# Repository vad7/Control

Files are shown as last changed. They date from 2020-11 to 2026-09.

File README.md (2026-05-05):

# ControlHeatPump
Контроллер теплового насоса

Открытый проект "Народный контроллер" для тепловых насосов.<br>
Данное програмноое обеспечение предназначено для управления<br>
различными типами тепловых насосов для отопления и ГВС.<br>
<br>
В данном репозитории идет текущая работа, возможны ошибки и нестабильная работа.<br>
Несколько оттестированный релиз здесь: https://github.com/vad7/ControlHeatPump<br>
<br>
Подробное обсуждение проекта на форуме: <br>
https://www.forumhouse.ru/threads/352693/ <br>
https://www.forumhouse.ru/threads/437182/ <br>
https://www.forumhouse.ru/threads/492563/<br>

Изменения по версиям: <br>
Версия 1.216<br>
1. Предварительный нагрев трассы котла по времени и по температуре, отложенное включение теплого пола по температуре
2. Доработка Modbus
3. рефакторинг кода
Версия 1.207<br>
1. Котел электрический или газовый. Управление через адаптер EctoControl RS485 (Modbus) или реле или Модбас реле. Возможность настроить раздельные цели для котла и ТН<br>
2. Динамические картинки на схеме.
3. Рефакторинг кода, оптимизация веба, отказ от семафоров RTOS, PID для охлаждения
4. Возможность греть бойлер только тэном
5. Мониторинг и информирования о ошибках и состояния нескольких BMS АКБ (входной программный UART на скорости 333 бод)
Версия 1.200<br>
1. Поддержка символьного дисплея 20x4 символов (LCD2004), может работать совместно с Nextion.<br>
2. ТН Воздух-Вода - полная поддержка, разморозка, установка оборотов компрессора и ЭРВ.<br>
3. Ежесуточные реле - переключение по температуре и по ночному тарифу<br>
4. Дамп ячеек Modbus, загрузка файла дампа в устройство Modbus<br>
5. Частотник Vacon: управление вентилятором, настройка мощности, контроль температуры, авто-сброс ошибки связи<br>
6. Дисплей Nextion: описание ошибки ТН текстом на главном экране<br>
7. Исправление множества ошибок в функциях: EEV, WR, Vacon, COP, Pumps, web<br>
8. Корректировка ЭРВ при переходе отопление-бойлер<br>
9. Опция включения циркуляционного насоса ГВС по расписанию<br>
10. Возможность изменять аварийные границы датчиков температур через веб<br>
11. Ограничение оборотов компрессора по времени<br>
12. ГВС: использовать только тэн во время "расписание только для тэна"<br>
13. Не считать статистику с меткой "во время работы" в переходных моментах бойлер-отопление и при возврате масла<br>
14. Статистика - отдельно считается тэн бойлера<br>
15. Пересоздание stats файлов при ошибке последовательности или длине=0<br>
16. Исправление работы насосов в паузе<br>
17. Исправление синхронизации времени, запрет смены часов во время работы ТН<br>
18. Исправление скролбара в веб<br>
19. Опция запрещать смену конкретного расписания<br>
20. Исправление безопасного доступа через веб, из-за кэширования он не работал адекватно<br>
21. Опция продолжения отопления после нагрева бойлера, если внутри гистерезиса<br>
22. Отображение на веб о включении суточных реле<br>
23. Корректировка минимальной мощности ваттроутера в зависимости текущей мощности с MPPT<br>
24. Поддержка двунаправленного электро-счетчика DDS238-2 ZN/S<br>
25. Настройки насосов отопления и дополнительного тэна перенесены в профили<br>
26. Новый режим работы дополнительного тэна на выходе ТН - интеллектуальный, теперь их три: по дому, по улице, интеллектуально<br>
27. Температура цели бойлера на схеме<br>
28. Корректировка датчиков WiFi (esp8266)<br>
29. Нагрев бойлера во время отсутствия электричества, если есть солнце<br>
30. Перенос настройки выключения насоса после останова компрессора в профили, отдельная задача по управлению насосами, чтобы была возможность контроля температур цели.<br>
31. Автопереключение режима работы - Отопление / Охлаждение<br>
32. Возможность использовать несколько периодов включения одного и того же ежесуточного реле.<br>
33. Возможность задать дополнительно любой датчик температуры как цель отопления. Расписание по часам контроля этих датчиков для каждого профиля.<br>
34. Догрев бойлера тэном во время паузы компрессора и низкой температуры или когда не смог нагреть с первого раза<br>
35. Управление теплым полом по датчикам теплого пола. Два режима - по превышению на заданную дельту целевой температуры или по целевой температуре датчика.<br>
36. Старт нагрева по минимальной температуре подачи.<br>
37. Максимальная температура цели для принудительного останова цикла нагрева, если по другим датчикам еще нужно греть.<br>
38. Поддержка частотников Danfoss VLT, Danfoss Micro Drive FC-51.<br>
39. Управления дополнительным солнечным подкачивающим инвертором (через реле).<br>
40. Подсчет потребления по дневному/ночному тарифу раздельно, опциональное.<br>

<br>
Версия 1.018-1.096<br>
1.  Исправление ошибок, оптимизация, доработка библиотек<br>
2.  Управления теплым полом (RPUMPFL), по выбранным датчикам температуры<br>
3.  Опции по догреву бойлера<br>
4.  Отправка SMS на smsc.ua, gate.smsclub.mobi<br>
5.  Для дисплея Nextion - cтраница изменения профилей, отображение реле бойлера, работа от генератора<br>
6.  Аналоговое или ШИМ управление частотником (используется класс VACON)<br>
7.  Добавлен Serial4<br>
8.  Загрузка веба на SD<br>
9.  Инвертор Омрон - обновление программирования и описания<br>
10. Отладка через Native USB порт (#define DEBUG_NATIVE_USB)<br>
11. Ежесуточное включение реле по расписанию (в режиме отопления)<br>
12. Поддержка электросчетчика PZEM-004T v3 (#define USE_PZEM004T)<br>
13. Добавлен режим работы ТН от резервного источника питания (генератора)<br>
14. Управление краном солнечного коллектора<br>
15. Улучшение режима супербойлера<br>
16. Поддержка NTC датчиков температуры (например: NTC 10K, B3435, резистор к VCC 15к)<br>
17. Вывод расширенной инфы по датчикам DS18B20<br>
18. Усиление на АЦП канале (x1,x2,x4) - #define ADC_GAIN<br>
19. Настройка графиков вынесена в конфиг, возможность изменить графики по датчикам во время работы<br>
20. Сохранение/восстановление настроек в bin всех профилей<br>
21. Работа от генератора: ограничение частоты, авто-определение источника<br>
22. Настройка погодозависимости целевой температуры<br>
23. Автопереключение расписаний по месяцам, погодозависимость<br>
24. Страницы помощи в веб<br>
25. Информирование по HTTP других контроллеров дома о работе от генератора<br>
26. Автозапуск генератора, гистерезис при работе от генератора<br>
27. Ваттроутер (PWM, реле, HTTP реле)<br>

Версия 0.967-1.017<br>
1.	Оптимизирован и уточнен алгоритм расчета температуры фреона по давлению<br>
2.	Фреон теперь задается через config.h (#define FREON)<br>
3.	Изменен формат TRANsADC[ANUMBER] в config.h, теперь целое число в тысячных<br>
4.	Отображение активного расписания<br>
5.	Добавлено инвертирование реверсивного клапана (#define INVERT_TRV)<br>
6.	Добавлен график переохлаждения<br>
7.	Контроль потока с учетом супербойлера<br>
8.	Настройка дельты включения СК<br>
9.	Документация на частотник по кнопке "?"<br>
10.	Переход на библиотеку SAM 1.6.12<br>
11.	Шаги закрытия ЭРВ задаются через #define EEV_CLOSE_STEP<br>
12.	Кнопка "подготовка к обновлению" - установка ЭРВ, сохранение буферов и т.д.<br>
13.	Для конфигурации без датчика высокого давления (PCON) добавление графиков "Конденсации" и "Нагнетание-конденсация"<br>
14.	Возврат масла для частотников Vacon<br>
15.	Отключение принудительной циркуляции ГВС при нагреве ГВС в режиме супербойлера<br>
16.	Очистка графиков при старте ТН (#define CLEAR_CHART_HP_ON)<br>
17.	Алгоритм прямого управления ЭРВ без ПИДа, контроль перегрева на входе компрессора<br>
18.	Защита от "заливания компресора"<br>
19.	Добавлена опция NO_MIN_EEV_CONTROL - При работе ПИД ЭРВ не контролировать достижение минимального открытия<br>
20.	График Нагнетание-Конденсация<br>
21.	Режим нагрева бойлера вместе с отоплением<br>
22.	Добавлено ограничение роста частоты ПИД регулятора<br>
23.	Графики поминутной работы на SD карте<br>
24.	Статистика по дням на SD карте, график с экспортом<br>
25.	Алгоритм 2 для ПИД регулятора (#define PID_FORMULA2)<br>
26.	Попытка восстановления соединений по модбасу перед пуском<br>
27.	Контроль останова частотника Vacon, уменьшение лога диагностики W5500<br>
28.	Проверка выключения инвертора ОМРОН через дискретный выход<br>
29.	Добавлена проверка исправности ЭРВ<br>
30.	Оптимизация задач RTOS<br>
31.	Подстройка температуры без смены профиля в расписаниях<br>
32.	Корректировка потребляемой мощности по включению реле<br>
33.	Исправление ошибок, оптимизация, доработка библиотек<br>
<br>
Версия 0.966<br>
1. Обновление текстовых файлов<br>
2. Добавлено описание ТН, исправлены ошибки для компиляции 1 конфига<br>
3. Работа над статистикой с записью ее на SD карту<br>
4. Фикс бага инициализации nextion если он находится в спящем режиме<br>
5. Мелкие уточнения в веб морде<br>
6. Обновление 2 конфига и уточнение типа ошибки при пуске компрессора<br>
7. Добавлен еще один алгоритм разморозки без датчика разморозки по температурам. Автор Pskovsat<br>
<br>
Версия 0.965<br>
1. Реализована возможность загрузки и работы с веб мордой на чипе spi flash.В опциях есть флаг загрузки из него<br>
2. Оптимизация работы АЦП<br>

Версия 0.964
1. Исправления ошибок в алгоритме работы ТН
2. Оптимизация работы АЦП
3. Оптимизация функции прерывания АЦП

Версия 0.963
1. Добавление spi диска
2. Частично сделана загрузка файлов через веб в spi диск (еще нужно причесать код и контроль ошибок)
3. Опция переключения места хранилища для веб-сервера
4. Доделка загрузки веб морды через веб в spi диск Есть проблемы при загрузке множества файлов (потеря пакетов)
5. Обновление дисплея Nextion, включая его прошивку
6. bugsfixs, добавлен редактор Nextion
7. Оптимизация длин неоторых запросов
8. Оптимизация стека RTOS

Версия 0.962
1. Изменены: структура сохранения, библиотека RTC, нумерация профилей в вебе, и др.
2. Nextion code changed
3. Nextion class rework
4. Исправлена ошибка с выводом сообщений при ошибках в классе HeatPump
5. Расписание теперь всегда компилится
6. Начало работы над загрузкой веб морды в spi Сделано декодирование имени и размера загружаемого файла
7. Сделан для post запросов разбор заголовка определение имени и длины файла и определение размеров первого (принятого) куска файла
8. Nextion update

Версия 0.961
1. Перенос SPI_RATE -> config.h
2. Замена библиотеки SdFat, функция тестирование скорости SD карты (/TEST_SPEED:<имя файла>)
3. Оптимизации библиотеки SdFat
4. Установка скорости SD в МГц - #define SD_CLOCK 24

Версия 0.960
1. Поддержка ИБП на контроллер
2. На страницу "Файлы" добавлены элементы для выбора файлов для копирования в spi eeprom
3. Исправлена ошибка с upload files
4. Имена аналоговых датчиков перенесены в config
5. Исправление ошибки вывода на график частотных датчиков
6. Добавлена опция - СК регенерирует ГК в простое ТН
7. Оптимизация закладки тест
8. Оптимизация СК, конфиг vad7, дефайн DEBUG_MODWORK
9. Настройки СК

Версия 0.959
1. Оптимизация web, выложена схема платы Добрыни
2. Замена в SDK DUE - добавлен класс UART
3. Исправлена ошибка с RPUMPBH
4. Исправлена ошибка с radio_sensor
5. Добавлена схема K-Line адаптера, небольшие фиксы
6. Исправлена ошибка с edit strings

Версия 0.958
1. Солнечный коллектор на плане (картинка)
2. Обновление первого конфига до текущей версии (cтарт-стоп компрессор с ТРВ переливная схема)
3. Включенное реле вручную на странице тестирование можно выключить только на ней, в не зависимости от текущей или будующей работы ТН.
4. Настройка через Config.h какие датчики температуры выводить на страницу "Схема", в const uint8_t SENSORTEMP[TNUMBER]={...} нужно поставить 2, у нужного датчика.
5. Изменение целевых температур бойлера и отопления на дельту по часам, для эффективного использования ночного тарифа
6. Условие расчета КОП (работа компрессора) определяется #define COP_ALL_CALC
7. На github выложена информация по дисплею Nextion
8. На github выложена информация по WiFi устройству (датчик температуры)
9. Проверка состояния частотника только перед его непосредственным стартом.
10. Добавлена опция "Однократный поиск "0" ЭРВ" Настройки ЭРВ из "Опций" перенесены в "Настройки ЭРВ"
11. Оптимизация парсера для вывода графика
12. "Причесывание" надписей на веб морде
13. Фикс бага для датчиков Wifi (откат формата uptime к виду 00d 00h 00m) Обновление морды удаленного датчика wifi
14. Оптимизация веб (датчики), температура
15. Поддержка радиодатчиков ZONT МЛ‑703

Версия 0.957
1. Опция "теплый пол" в профилях - управляет насосом RPUMPFL
2. Опция - расписание ГВС только для ТЭНа бойлера
3. Изменение режима турбо ГВС. Теперь при включении турбо+догрев ГВС греетеся ТН+ТЭН до температуры догрева далее только ТЭН
4. Фикс работы насосов (в схеме без трехходового) для режима пауза
5. Чтение настроек из файла (в новом формате)
6. Фикс алгоритма Сальмоннеллы
7. Фикс блокировки семафорора для 485 порта (уменьшена загрузка CPU при работе ТН)
8. Фикс сброса сетевой карты
9. Добавлена возможность работы с солнечным/воздушным коллектором (#define USE_SUN_COLLECTOR)

Версия 0.956
1. Оптимизирована запись в журнал, радиодатчики - начало.
2. max/min sensorADC
3. Включение RPUMPO при переключение с бойлера на отопление
4. Фикс ошибки при выходе из нагрева ГВС при срабатывании защиты
5. Cохранение в файл в новом формате
6. Опция логировать работу частотника
7. Фикс при переходе нагрева бойлера на тэн
8. Опциональное вычисление для TIN среднего и/или минимального значения среди других датчиков
9. Фикс расчета перегрева при охлаждении, фикс работы бойлера (переключение на дом)

Версия 0.955
1. Оптимизация работы oneWire
2. Ускоренный поиск датчиков температуры
3. Неограниченное кол-во DS18x20, исправление ошибки в DUE UART

Версия 0.954
1. Оптимизация графиков
2. Ethernet lib fix (зацикливание при передаче MQTT)
3. Расчет графиков powerCO powerGEO на лету, фикс вывода графиков в файл
4. Синхронизация времени по HTTP GET с esp8266 веб-сервера (отдельное устройство vad711),
5. Изменен блок статусов, опция не проверять CRC у DS18B20, изменены единицы работы насосов в паузе на сек, изменены настройки датчиков протока, багфиксы.
6. Индикация тэна и насоса бойлера на странице схема, багфиксы
7. Возможность использовать 4 шины датчиков температуры, 3 из них могут быть двухпроводные.
8. В файл настроек в текстовом виде, добавлен вывод новых (пропущеных) параметров
9. Доработка по шинам температуры на DS2482, добавлен режим чтения аналоговых датчиков через модбас
10. Фикс разморозки воздушника + описание в части датчиков температуры
11. Сохранение без потери настроек при изменении структуры
12. Поддержка датчиков ds18s20

Версия 0.953
1. Веб морда добаление дополнительных параметров на схему ТН
2. Возможность скрытия логирования ошибок чтения счетчика SDM120
3. Оптимизация библиотеки Модбас в части работы с портом
4. Дополнительные флаги для датчиков температуры (логирование и игнорирование ошибок)
5. Оптимизация чтения датчиков и modbus, вывод частоты сети 220 в веб.
6. Вывод мощности CO, доработка Vacon
7. Доработка корректировки перегрева, исправление ошибок  модбас, ваком
8. Оптимизация парсера - удаление из парсеров параметров которые только на чтение
9. Фикс восстановления настроек инвертора Омрон (флаги)
10. Небольшие переделки страницы ЭРВ
11. Добавлен график 20, 30 сек, небольшая оптимизация парсера
12. Фикс для охлаждения датчик TCONOUT и фикс расчета мощностей и СОРов для охлаждения
13. Доработка корректировки перегрева
14. Оптимизации работы с ftoa itoa, удаление функции int2str
15. В config настройка задержки после переключения насосов
16. Оптимизация чтения счетчика SDM
17. Оптимизация функций DecodeTimeDate и StatDate, фикс ошибок парсера реле
18. Фикс ошибки старта насоса при догреве(только)
19. Расчет мощностей и СОР всегда (раньше было только при работе)
20. Vacon расчет номинальной мощности
21. Доработка страницы ЭРВ, фикс ПИД эрв
22. фикс передачи на MQTT сервер
23. Мощность частотника в Вт
24. Vacon - авто-очистка сбоя, очередь из 1 команды, оптимизация, раздельный останов насосов по дефайну и др.
25. Возможность выключить ТН из отложенного запуска/рестарт по ошибке
26. Для Омрона отдельная страница настроек (гц) - надо копировать
27. Перенос флага включения ТН в счетчики, теперь профиль реже пишутся
28. Дельта коррекции перегрева считается от стартового перегрева

Версия 0.952
1. Добавлено в управление ЭРВ возможность корректировки перегерва в зависмости от разницы температур испарителя и конденсатора
2. Оптимизация сохранения ЭРВ
3. Фикс: DHСP, датчики температуры. Оптимизация веба.
4. Опция - один датчик на 2-ой шине 1-Wire, для уменьшения влияния помех (измененен формат сохранения: 123)
5. DNS по TCP (выбор автоматически), доработка сетевой либы, оптимизация журнала и др.
6. Начало переделки парсера запросов с целью его оптимизации и увеличения скорости.
7. В класс ЭРВ добавлы настройки (из дефайнов) и оптимизировано сохранение (единая структура настроек)
8. В класс FC добавлы настройки (из дефайнов) и оптимизировано сохранение (единая структура настроек) (измененен формат сохранения: 125)
9. В опции ТН добавлены настройки времен, парсер опций переделан

Версия 0.951
1. Доработка веб, перенос настроек в config, исправление багов
2. Доработка страницы тестирования
3. Добавлен расчет переохлаждение на схеме ТН

Версия 0.950
1. Доработка 1-Wire, багфиксы, новая ошибка ERR_ONEWIRE_RW - ошибка во время чтения/записи OneWire
2. Фикс библиотеки DUE для доступности портов D53,D69
3. Доработка I2C init
4. Оптимизация Web-modbus

Версия 0.949
1. Оптимизация использования стека в itoa, vsnprintf, ftoa cj,собсвенная функция printf
2. Patch Arduino board SAM library for optimized itoa() function
3. Добавлен насос нагрева ГВС RPUMPBH (не циркуляции ГВС)
4. Фикс отображения включения ТН во время паузы
5. Добавлена кнопка сброса статистики задач free RTOS
6. Исправлена ошибка перехода в режим Ожидания по расписанию
7. Для экономии памяти теперь графики расчета разности температур ПТО рассчитываются в момент запроса
8. Добавлен насос теплых полов RPUMPFL (в режиме охлаждения не включается)
9. Перевод FLOWPCON в не обязательный параметр
10. Автоскрытие аналогового управления инвертером, насоса ТП
11. Доработка по инвертору Vacon (режим тест)

Версия 0.948
1. Уменьшение потребление стека RTOS
2. Фикс ожидания DHCP, оптимизация сетевой либы

Версия 0.947
1. При инициализации сетевого чипа добавлена проверка на соединение сетевым кабелем (link)
2. Переделан код обслуживания ТЭНа бойлера, теперь он сосредоточен в одном месте
3. Оптимизация и переименование кода для переключения между ГВС и отоплением/охлаждением (поддержка управления насосами для переключения)
4. Исправлена ошибка с сохранением/восстановлением настроек в бинарный файл
5. Доделана и протестирована страница Modbus (можно читать/сохранять регистры)
6. Сделан алгоритм обеззараживания (сальмонелла) для ГВС
7. Исправлена ошибка в расписании ГВС

Версия 0.946
1. Исправлена ошибка отображения графика потока конденсатора
2. Исправлена ошибка вывода в текстовый файл настроек (коэффициент для аналогового датчика)
3. Исправлена ошибка управленем догревом бойлера - алгоритм перенесен в другое место
4. Исправлена ошибка в режиме тест для датчиков потока
5. Настройки догрева бойлера перенесены в раздел ГВС из опций (откорректированы имена параметров запросов)
6. Сделан вывод специфических ошибок для Vacon 10 и пофиксены некоторые ошибки
7. Добавлена возможность проверки потоков на минимальные значения перед включением компрессора (#define FLOW_CONTROL)
8. Доработана морда для сканирования после изменения работы шины OneWire, в новой версии увеличилось время сканирования.
9. Дмитрий обновил мобильную морду
10. Добавлен функционал модификации имен запрашиваемых файлов, теперь в зависимости от конфига показываются на морде разные схемы.
11. В работу ТН добавлены внутренние команды WAIT и RESUME для обеспечения функционала расписания, теперь если в расписании дырка (нет профайла) то ТН будет находится в сосоянии "Ожидание"
12. ТЕСТ страничка с чтением/записью произвольных ячеек Modbus RTU

Версия 0.945
1. R3WAY переведен в необязательный, теперь можно компилировать без него
2. При переключениеи с ГВС сделано временное отключение (#define DELAY_BOILER_OFF) части защит, на время остывания ТН.
3. Немного переделана функция вывода ошибок, теперь где актуально выводится имя функции в которой произошла ошибка
4. В уведомлениях почты убран вывод устройство которых нет в текущей конфигурации (если стоит флаг выводить подробности)
5. Исправлен и добавлен вывод настроек ТН в текстовом виде (дабавлены настроки тарифов)
6. Проведено переименование констант, переменных и функция инвертора  в нейтральные (без упоменния ОМРОН и МХ2)
7. Добавлена поддержка трехфазного счетчика SDM630 (vad711) (определить #define USE_SDM630)
8. Класс частотный преобразователь был стандартизован (все аппартано зависимые функции спрятаны внутрь класса) для возможности подключения других инверторв короме Omrona
9. vad711 добавил поддержку инвертора Vacon 10 по модбасу.
10. Исправлена ошибка подсчета общего числа ошибок чтения датчиков температуры
11. Переделана блокировка задачи циркуляционного насоса отопления в паузах
12. Исправлена ошибка вывода информации при старте ТН
13. Переделан механизм работы с датчиками температуры. Теперь разрешено три вида шин OneWire и одновременно может присутвовать три вида шин в контроллере.
14. Добавлено расписание работы (пока не до конца)
15. Переделан вид расписания бойлера на веб морде
16. Добавлена страница на вебморду для вывода информации по задачам операционной системы (главное - минимальный размер стека)
17. Часть нагрузки из задачи "бездействия" перенесено в задачу чтения датчиков
18. На морде в профилях сделано обновление данных при изменении параметров профиля
19. В связи с работой над расписаниями, удален функционал тарифов день/ночь
20. Исправена ошибка вывода числа ошибок чтения температурных датчиков.
21. Добавлен ввод теплоемкости теплоносителя в контурах где стоят расходомеры (изменилась версия сохранения)
22. Переделана размерность коэффициентов пересчета расходомеров, теперь она в имп/литр

Скриншеты веб-интерфейса:

Состояние
Схема
ЭРВ
Настройки
Расписание
Датчики
Реле
Инвертор
RTOS
Графики
Графический лог
Статистика
Ваттроутер

Выносной экран Nextion:

Nextion Main
Nextion Scheme
Nextion Heat

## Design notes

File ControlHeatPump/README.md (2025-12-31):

# Control
Heat pump full repository

<br>
<b>Ver. 1.207<b>

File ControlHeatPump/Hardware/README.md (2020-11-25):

# ControlHeatPump
Файлы которые надо заменить в стандартном SDK Due (смотрите путь к файлам начиная с hardware)<br>
Библиотека DUE SAM: https://github.com/arduino/ArduinoCore-sam

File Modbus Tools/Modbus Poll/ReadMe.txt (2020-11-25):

------------------------------------------------------------------------------------
                       Modbus Poll
         Copyright (c) 2002-2017. Witte Software.
------------------------------------------------------------------------------------

Getting started:
-----------------------------
1. Press F3 to setup a connection.
2. Press F8 to setup protocol definition.
   Example:
   You want to read 20 holding registers from address 40011 (10).
   - Slave ID  = The ID of your device
   - Function  = 03 Read Holding Registers
   - Address   = 10 (Protocol address)
   - Quantity  = 20
   - Scan Rate = 1000 (Then it will poll for data every 1000ms)

3. To change a value just start typing or double click the cell.

Note: You can always press F1 for help.

Warning:
-----------------------------
The use of RTS controlled RS232/RS485 converters should be avoided if possible.
It is difficult to determine the exact time when to switch off the transmitter
with non real-time operating systems like Windows and Linux. If it is switched
off to early characters might still sit in the FIFO or the transmit register of
the UART and these characters will be lost. Hence the slave will not recognize
the message. On the other hand if it is switched off too late then the slave's
message is corrupted and the master will not recognize the message.

Modbus Poll overview:
-----------------------------
Modbus Poll is a powerful, easy to use, master simulating
tool. Modbus Poll will run on all 32/64-bit Windows versions
in use today - XP, Vista, 7, 8, 8.1 and 10.

With Modbus Poll you can monitor and test your modbus
slave devices. Some of the features:
- Supports Modbus/TCP, RTU and ASCII modes.
- Test Center for modbus slave developers.
- OLE Automation for interfacing with Visual Basic
  Excel etc. To interpret and show the modbus data
  according to your specific requirements. E.g. edit
  data in Excel and then send to your slave!
- Multiple windows for monitoring of multiple
  slaves/data areas.
- Monitoring of serial traffic.
- Data logging to a text file.
- Data logging to MS Excel.
- Multithreated for best performance.
- Print preview etc.
- 16 Display formats.

Press F2 or double click to edit or just start typing a new value.

Order information:
-----------------------------
Visit http://www.modbustools.com

Technical Support:
-----------------------------
Your feedback is very important for the further development
of Modbus Poll. For bug reports, comments, suggestions or
complaints, please find contact information at
http://www.modbustools.com

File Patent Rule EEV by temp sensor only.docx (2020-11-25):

# http://www.patentsencyclopedia.com/app/20120260678

# Patent application title: AIR CONDITIONER, METHOD FOR CONTROLLING OPENING OF EXPANSION VALVE, AND COMPUTER-READABLE RECORDING MEDIUM WITH EXPANSION VALVE OPENING CONTROL PROGRAM RECORDED THEREON

Inventors: Michiho Yoshida (http://www.patentsencyclopedia.com/inventor/yoshida-osaka-shi-4/) (Osaka-Shi, JP)
IPC8 Class: AF25B4104FI
USPC Class: 62 56
Class name: Refrigeration processes (http://www.patentsencyclopedia.com/class/000419133)
Publication date: 2012-10-18
Patent application number: 20120260678

## Abstract:

An air conditioner includes: a compressor for compressing a refrigerant; an expansion valve for adjusting the flow of the refrigerant; a first temperature sensor for detecting a discharge temperature of the compressor; and a second temperature sensor for detecting a temperature of a condenser. A discharge temperature difference is calculated that is a difference between the discharge temperature detected by the first temperature sensor and the temperature of an outdoor heat exchanger or an indoor heat exchanger functioning as the condenser that is detected by the second temperature sensor. The opening of the expansion valve is set based on the calculated discharge temperature difference and a target discharge temperature difference that is set so that a target degree of superheat is obtained.

## Claims:

1. An air conditioner comprising: a compressor for compressing a refrigerant; an expansion valve for adjusting a flow of said refrigerant; a first temperature sensor for detecting a discharge temperature of said compressor; a second temperature sensor for detecting a temperature of a condenser;and control means for controlling an opening of said expansion valve, said control means calculating a discharge temperature difference which is a difference between said discharge temperature detected by said first temperature sensor and the temperature of said condenser detected by said second temperature sensor, and said control means setting a basic opening which is an opening of said expansion valve under normal control, based on said calculated discharge temperature difference and a target discharge temperature difference (TMP_aim) that is set so that a target degree of superheat is obtained.

2. The air conditioner according to claim 1, wherein when said calculated discharge temperature difference is not less than a predetermined first threshold value (Hth), said control means controls the opening of said expansion valve so that the opening is larger than said basic opening under said normal control.

3. The air conditioner according to claim 2, wherein when said calculated discharge temperature difference is not more than a predetermined second threshold value (Lth), said control means controls the opening of said expansion valve so that the opening is smaller than said basic opening under said normal control, and said second threshold value is smaller than said first threshold value.

4. The air conditioner according to claim 1, wherein when said calculated discharge temperature difference is not more than a predetermined second threshold value (Lth), said control means controls the opening of said expansion valve so that the opening is smaller than said basic opening under said normal control.

5. The air conditioner according to claim 1, wherein said control means calculates said target discharge temperature difference (TMP_aim) from the number of revolutions of said compressor.

6. The air conditioner according to claim 1, further comprising: a switch valve for switching direction of circulation of said refrigerant between a cooling cycle operation and a heating cycle operation; an outdoor heat exchanger for heat exchange between outdoor air and said refrigerant; and an indoor heat exchanger for heat exchange between indoor air and said refrigerant, wherein in the cooling cycle operation, said condenser corresponds to said outdoor heat exchanger and, in the heating cycle operation, said condenser corresponds to said indoor heat exchanger.

7. A method for controlling an opening of an expansion valve of an air conditioner, said air conditioner including: said expansion valve for adjusting a flow of a refrigerant; a first temperature sensor for detecting a discharge temperature of a compressor; and a second temperature sensor for detecting a temperature of a condenser, said method comprising the steps of: calculating a discharge temperature difference which is a difference between said discharge temperature detected by said first temperature sensor and the temperature of said condenser detected by said second temperature sensor; and setting a basic opening which is an opening of said expansion valve under normal control, based on said calculated discharge temperature difference and a target discharge temperature difference (TMP_aim) that is set so that a target degree of superheat is obtained.

8. A computer-readable recording medium with an expansion valve opening control program recorded thereon for causing a computer provided to an air conditioner including: an expansion valve for adjusting a flow of a refrigerant; a first temperature sensor for detecting a discharge temperature of a compressor; and a second temperature sensor for detecting a temperature of a condenser, to perform the steps of: calculating a discharge temperature difference which is a difference between said discharge temperature detected by said first temperature sensor and the temperature of said condenser detected by said second temperature sensor; and setting a basic opening which is an opening of said expansion valve under normal control, based on said calculated discharge temperature difference and a target discharge temperature difference that is set so that a target degree of superheat is obtained.

9. The air conditioner according to claim 2, wherein said control means calculates said target discharge temperature difference (TMP_aim) from the number of revolutions of said compressor.

10. The air conditioner according to claim 3, wherein said control means calculates said target discharge temperature difference (TMP_aim) from the number of revolutions of said compressor.

11. The air conditioner according to claim 4, wherein said control means calculates said target discharge temperature difference (TMP_aim) from the number of revolutions of said compressor.

12. The air conditioner according to claim 2, further comprising: a switch valve for switching direction of circulation of said refrigerant between a cooling cycle operation and a heating cycle operation; an outdoor heat exchanger for heat exchange between outdoor air and said refrigerant; and an indoor heat exchanger for heat exchange between indoor air and said refrigerant, wherein in the cooling cycle operation, said condenser corresponds to said outdoor heat exchanger and, in the heating cycle operation, said condenser corresponds to said indoor heat exchanger.

13. The air conditioner according to claim 3, further comprising: a switch valve for switching direction of circulation of said refrigerant between a cooling cycle operation and a heating cycle operation; an outdoor heat exchanger for heat exchange between outdoor air and said refrigerant; and an indoor heat exchanger for heat exchange between indoor air and said refrigerant, wherein in the cooling cycle operation, said condenser corresponds to said outdoor heat exchanger and, in the heating cycle operation, said condenser corresponds to said indoor heat exchanger.

14. The air conditioner according to claim 4, further comprising: a switch valve for switching direction of circulation of said refrigerant between a cooling cycle operation and a heating cycle operation; an outdoor heat exchanger for heat exchange between outdoor air and said refrigerant; and an indoor heat exchanger for heat exchange between indoor air and said refrigerant, wherein in the cooling cycle operation, said condenser corresponds to said outdoor heat exchanger and, in the heating cycle operation, said condenser corresponds to said indoor heat exchanger.

## Description:

TECHNICAL FIELD

[0001] The present invention relates to an air conditioner as well as a method and a program for controlling the opening of an expansion valve, and particularly to an air conditioner adjusting the flow of a refrigerant by controlling the opening of an expansion valve, as well as a method and a program for controlling the opening of an expansion valve.

BACKGROUND ART

[0002] Generally, an air conditioner includes components such as a compressor, a four-way (switch) valve, an outdoor heat exchanger, an expansion valve for adjusting the flow of a refrigerant when reducing the pressure, and an indoor heat exchanger. Such an air conditioner is capable of performing both the cooling cycle operation and the heating cycle operation by switching the four-way valve. When the cooling cycle operation is done, the piping connection is made to configure a refrigerant flow path (cooling cycle) in which the refrigerant circulates through the components in the order of the compressor, the four-way valve, the outdoor heat exchanger (condenser), the expansion valve, the indoor heat exchanger (evaporator), the four-way valve, and the compressor. Thus, the heat absorbed by the indoor heat exchanger is released outdoors by the outdoor heat exchanger. In contrast, when the heating cycle operation is done, the piping connection is made to configure a refrigerant flow path (heating cycle) in which the refrigerant circulates through the components in the order of the compressor, the four-way valve, the indoor heat exchanger (condenser), the expansion valve, the outdoor heat exchanger (evaporator), the four-way valve, and the compressor. Thus, the outdoor heat absorbed by the outdoor heat exchanger is released into the room by the indoor heat exchanger.

[0003] When the heat exchange cycle as described above is formed, generally the evaporator temperature and the evaporator outlet temperature are detected to thereby calculate the degree of superheat, and the degree of superheat is used to control the opening of the expansion valve.

[0004] Another method for controlling the expansion valve is disclosed in PTL 1, according to which the inlet temperature of the expansion valve and the outlet temperature of the expansion valve (or the inlet temperature of the evaporator) are detected to estimate the evaporation saturation temperature. From the estimated evaporation saturation temperature and a set degree of superheat, a target suction temperature of the compressor is determined. The opening of the expansion valve is controlled so that the suction temperature of the compressor meets the target suction temperature.

[0005] PTL 2 discloses that the opening of the expansion valve is controlled in accordance with a temperature difference between the temperature of the refrigerant at the discharge of the compressor and an optimum temperature of the refrigerant at the discharge which is calculated based on the evaporation temperature and the condensation temperature.

CITATION LIST

Patent Literature

[0006] PTL 1: Japanese Patent Laying-Open No. 7-98160 [0007] PTL 2: Japanese Patent Laying-Open No. 4-93541

SUMMARY OF INVENTION

Technical Problem

[0008] In the case where the evaporator temperature and the evaporator outlet temperature are used for calculating the degree of superheat, temperature sensors such as thermistors have to be provided respectively at the inlet and the outlet of the evaporator.

[0009] Even in such a case as PTL 1 where the degree of superheat is estimated without detecting the evaporator temperature, a separate thermistor or the like is necessary for detecting the suction temperature of the compressor.

[0010] According to PTL 2, the temperature of the refrigerant at the discharge of the compressor, the evaporation temperature, and the condensation temperature are detected to control the opening of the expansion valve. PTL 2 thus does not disclose that the opening of the expansion valve is controlled based on a temperature difference between two locations.

[0011] The present invention has been made to solve the above-described problems, and an object of the present invention is to provide an air conditioner capable of appropriately controlling the opening of the expansion valve without increasing the number of temperature sensors, as well as a method and a program for controlling the opening of the expansion valve.

Solution to Problem

[0012] An air conditioner according to an aspect of the present invention includes: a compressor for compressing a refrigerant; an expansion valve for adjusting a flow of the refrigerant; a first temperature sensor for detecting a discharge temperature of the compressor; a second temperature sensor for detecting a temperature of a condenser; and control means for controlling an opening of the expansion valve. The control means calculates a discharge temperature difference which is a difference between the discharge temperature detected by the first temperature sensor and the temperature of the condenser detected by the second temperature sensor, and sets a basic opening which is an opening of the expansion valve under normal control, based on the calculated discharge temperature difference and a target discharge temperature difference that is set so that a target degree of superheat is obtained.

[0013] Preferably, when the calculated discharge temperature difference is not less than a predetermined first threshold value, the control means controls the opening of the expansion valve so that the opening is larger than the basic opening under the normal control.

[0014] Preferably, when the calculated discharge temperature difference is not more than a predetermined second threshold value, the control means controls the opening of the expansion valve so that the opening is smaller than the basic opening under the normal control. The second threshold value is smaller than the first threshold value.

[0015] Preferably, the control means calculates the target discharge temperature difference from the number of revolutions of the compressor.

[0016] Preferably, the air conditioner further includes: a switch valve for switching direction of circulation of the refrigerant between a cooling cycle operation and a heating cycle operation; an outdoor heat exchanger for heat exchange between outdoor air and the refrigerant; and an indoor heat exchanger for heat exchange between indoor air and the refrigerant. In the cooling cycle operation, the condenser corresponds to the outdoor heat exchanger. In the heating cycle operation, the condenser corresponds to the indoor heat exchanger.

[0017] According to another aspect of the present invention, a method for controlling an opening of an expansion valve of an air conditioner is provided. The air conditioner includes: the expansion valve for adjusting a flow of a refrigerant; a first temperature sensor for detecting a discharge temperature of a compressor; and a second temperature sensor for detecting a temperature of a condenser. The method includes the steps of: calculating a discharge temperature difference which is a difference between the discharge temperature detected by the first temperature sensor and the temperature of the condenser detected by the second temperature sensor; and setting a basic opening which is an opening of the expansion valve under normal control, based on the calculated discharge temperature difference and a target discharge temperature difference that is set so that a target degree of superheat is obtained.

[0018] According to still another aspect of the present invention, a computer-readable recording medium with an expansion valve opening control program recorded thereon is provided. The expansion valve opening control program causes a computer, which is provided to an air conditioner including: an expansion valve for adjusting a flow of a refrigerant; a first temperature sensor for detecting a discharge temperature of a compressor; and a second temperature sensor for detecting a temperature of a condenser, to perform the steps of: calculating a discharge temperature difference which is a difference between the discharge temperature detected by the first temperature sensor and the temperature of the condenser detected by the second temperature sensor; and setting a basic opening which is an opening of the expansion valve under normal control, based on the calculated discharge temperature difference and a target discharge temperature difference that is set so that a target degree of superheat is obtained.

Advantageous Effects of Invention

[0019] In accordance with the present invention, the opening of the expansion valve is set based on: the difference between the compressor discharge temperature and the condenser temperature (discharge temperature difference); and the target discharge temperature difference that is set so that a target degree of superheat is obtained. Accordingly, the opening of the expansion valve can appropriately be controlled without increase of the number of temperature sensors.

BRIEF DESCRIPTION OF DRAWINGS

[0020] FIG. 1 is a diagram schematically showing a refrigerant circuit of an air conditioner in an embodiment of the present invention.

[0021] FIG. 2 is an external view of an indoor unit of an air conditioner in an embodiment of the present invention.

[0022] FIG. 3 (http://www.patentsencyclopedia.com/imgfull/20120260678_03) is a cross-sectional view schematically showing an internal configuration of the indoor unit shown in FIG. 2.

[0023] FIG. 4 (http://www.patentsencyclopedia.com/imgfull/20120260678_03) is an external view of an outdoor unit of an air conditioner in an embodiment of the present invention.

[0024] FIG. 5 (http://www.patentsencyclopedia.com/imgfull/20120260678_04) is a diagram schematically showing an internal configuration of the outdoor unit shown in FIG. 4 (http://www.patentsencyclopedia.com/imgfull/20120260678_03).

[0025] FIG. 6 (http://www.patentsencyclopedia.com/imgfull/20120260678_05) is a functional block diagram showing a functional configuration of an air conditioner in an embodiment of the present invention.

[0026] FIG. 7 (http://www.patentsencyclopedia.com/imgfull/20120260678_06) is a diagram showing an example of a Mollier diagram (P-h diagram).

[0027] FIG. 8 (http://www.patentsencyclopedia.com/imgfull/20120260678_07) is a diagram showing a relation between a target discharge temperature difference and each threshold value, and the number of revolutions of a compressor in an embodiment of the present invention.

[0028] FIG. 9 is a flowchart showing a process of calculating a target opening in an embodiment of the present invention.

DESCRIPTION OF EMBODIMENTS

[0029] An embodiment of the present invention will be described in detail with reference to the drawings. In the drawings, the same or corresponding components are denoted by the same reference characters, and a description thereof will not be repeated.

[0030] <As to Refrigerant Circuit>

[0031] First, an example of a refrigerant circuit of an air conditioner in the present embodiment will be described.

[0032] FIG. 1 is a diagram schematically showing the refrigerant circuit of the air conditioner in the embodiment of the present invention.

[0033] Referring to FIG. 1, the air conditioner includes a heat exchanger 1 for an outdoor unit (hereinafter referred to as "outdoor heat exchanger"), an expansion valve 2, a heat exchanger 3 for an indoor unit (hereinafter referred to as "indoor heat exchanger"), a four-way valve 4, and a compressor 5. They are connected in order in the form of a closed loop. Compressor 5 compresses a refrigerant. Outdoor heat exchanger 1 transfers heat between the outdoor air and the refrigerant. Expansion valve 2 is controlled for adjusting the flow of the refrigerant. Indoor heat exchanger 3 transfers heat between the indoor air and the refrigerant. Four-way valve 4 switches the direction in which the refrigerant circulates, depending on whether the operation is the cooling cycle operation or the heating cycle operation.

[0034] The air conditioner further includes a temperature sensor 6 for measuring the temperature of outdoor heat exchanger 1, a temperature sensor 7 for measuring the discharge temperature of compressor 5, and a temperature sensor 8 for measuring the temperature of indoor heat exchanger 3. These temperature sensors 6, 7, 8 are, for example, thermistors.

[0035] As indicated by an arrow in FIG. 1, when the cooling cycle operation is performed, the refrigerant circulates through compressor 5, four-way valve 4, outdoor heat exchanger 1, expansion valve 2, indoor heat exchanger 3, four-way valve 4, and compressor 5 in this order. In this case, outdoor heat exchanger 1 functions as a condenser for condensing and liquefying the compressed refrigerant of a high temperature, and indoor heat exchanger 3 functions as an evaporator for evaporating the liquefied refrigerant to thereby convert the refrigerant into a low-temperature gas. When the heating operation is performed, the refrigerant circulates through compressor 5, four-way valve 4, indoor heat exchanger 3, expansion valve 2, outdoor heat exchanger 1, four-way valve 4, and compressor 5 in this order. In this case, outdoor heat exchanger 1 functions as an evaporator and indoor heat exchanger 3 functions as a condenser.

[0036] While the present embodiment will be described in which the heating cycle operation and the cooling cycle operation can be switched to each other, the air conditioner may be capable of only one of the heating cycle operation and the cooling cycle operation. In this case, outdoor heat exchanger 1 and indoor heat exchanger 3 each function solely as a condenser or an evaporator.

[0037] <External Appearance and Configuration>

[0038] As to indoor unit:

[0039] FIG. 2 is an external view of an indoor unit 100 of the air conditioner in the embodiment of the present invention. FIG. 3 (http://www.patentsencyclopedia.com/imgfull/20120260678_03) is a cross-sectional view schematically showing an internal configuration of indoor unit 100 in FIG. 2. In FIG. 3 (http://www.patentsencyclopedia.com/imgfull/20120260678_03), a cross section of indoor unit 100 as seen in the direction of the Y axis in FIG. 2 is shown.

[0040] Referring to FIG. 3 (http://www.patentsencyclopedia.com/imgfull/20120260678_03), indoor unit 100 further includes, in addition to indoor heat exchanger 3 and temperature sensor 8 shown in FIG. 1, a temperature sensor 11 for measuring the room temperature, an indoor fan 14, a louver 15, and a louver motor 16. Louver 15 is a wind direction guide member provided in an air outlet of indoor unit 100. Louver motor 16 drives louver 15 so that louver 15 turns. A plurality of louvers 15 are driven so that they are identically oriented.

[0041] As to outdoor unit:

[0042] FIG. 4 (http://www.patentsencyclopedia.com/imgfull/20120260678_03) is an external view of an outdoor unit 200 of the air conditioner in the embodiment of the present invention. FIG. 5 (http://www.patentsencyclopedia.com/imgfull/20120260678_04) is a diagram schematically showing an internal configuration of outdoor unit 200 in FIG. 4 (http://www.patentsencyclopedia.com/imgfull/20120260678_03).

[0043] Referring to FIG. 5 (http://www.patentsencyclopedia.com/imgfull/20120260678_04), outdoor unit 200 includes, in addition to outdoor heat exchanger 1, four-way valve 4, compressor 5, and temperature sensor 6 shown in FIG. 1, a temperature sensor 21 for measuring the outdoor air temperature, and an outdoor fan 24.

[0044] As to functional configuration of air conditioner:

[0045] FIG. 6 (http://www.patentsencyclopedia.com/imgfull/20120260678_05) is a functional block diagram showing a functional configuration of the air conditioner in the embodiment of the present invention.

[0046] Referring to FIG. 6 (http://www.patentsencyclopedia.com/imgfull/20120260678_05), the air conditioner further includes, in addition to the components shown in FIGS. 1, 3, and 5, a stepper motor 12 driven for adjusting the opening of expansion valve 2, a control unit 30 for controlling the whole air conditioner, and an operation unit 36 for receiving instructions from a user. In the present embodiment, the opening of expansion valve 2 is calculated as corresponding to the number of excitation steps for the phases of stepper motor 12. It is noted that expansion valve 2 is not limited to the expansion valve whose opening is adjusted by stepper motor 12, and may be a thermostatic expansion valve, for example. Specifically, a feeler bulb in which the refrigerant is enclosed and the expansion valve are connected by a capillary tube, and the inside of the expansion valve is partitioned by a diaphragm. The opening of the expansion valve may also be controlled by means of the pressure that is applied to the diaphragm depending on the temperature of the feeler bulb.

[0047] Control unit 30 is contained in indoor unit 100 and includes a processor 32 for performing various operations, and a memory 34 for storing various programs and data. Processor 32 is configured for example by a CPU (Central Processing Unit). Processor 32 executes a program stored in memory 34 to thereby control the opening of expansion valve 2 as described later herein. Memory 34 may for example be a nonvolatile memory such as flash memory.

[0048] Operation unit 36 includes, for example, a power switch, a temperature adjustment key, an air volume adjustment key, and a timer set key.

[0049] The air conditioner may further include an interface unit 38 for reading/writing data/program from/in a computer-readable non-transitory recording medium 38a. Processor 32 stores in memory 34 the program read by interface unit 38 from recording medium 38a (or updates an existing program) to thereby perform control of the opening of expansion valve 2 as described later herein (a process of calculating the opening). Recording medium 38a includes, for example, an optical medium such as CD-ROM (Compact Disc-ROM) and a magnetic recording medium such as memory card.

[0050] As to control of expansion valve:

[0051] A description will be given of control (control of the opening) of expansion valve 2 performed by control unit 30 (processor 32) in the present embodiment.

[0052] Generally, in order to efficiently perform heat exchange in each cycle, the opening of the expansion valve is often controlled by means of the degree of superheat which is calculated from the outlet temperature of the evaporator. Actually, the evaporator temperature and the evaporator outlet temperature are detected and control is performed so that the temperature difference between the evaporator temperature and the evaporator outlet temperature is a target degree of superheat. "Degree of superheat" represents a temperature difference between a superheated vapor temperature and a dry saturated vapor temperature at a certain pressure.

[0053] In the present embodiment as well, the degree of superheat is used to control expansion valve 2. The target degree of superheat, however, is estimated in the present embodiment from a temperature difference (TMP_diff) between a discharge temperature (TMP_to) and a condenser temperature (TMP_con).

[0054] As described above, conventionally the degree of superheat is usually calculated from the evaporator temperature and the evaporator outlet temperature. However, since a compression line on a Mollier diagram is determined by the compression pressure (corresponding to the number of revolutions) of compressor 5, control can also be performed by means of a difference between the discharge temperature and the condenser temperature (the difference will hereinafter be referred to as "discharge temperature difference") similarly to the control using the difference between the evaporator temperature and the evaporator outlet temperature. This will be described in more detail with reference to FIG. 7 (http://www.patentsencyclopedia.com/imgfull/20120260678_06).

[0055] FIG. 7 (http://www.patentsencyclopedia.com/imgfull/20120260678_06) is a diagram showing an example of the Mollier diagram (P-h diagram). In the Mollier diagram, a relation between the pressure (kg/dm2) and the enthalpy (kcal/kg) is shown.

[0056] In FIG. 7 (http://www.patentsencyclopedia.com/imgfull/20120260678_06), the closed loop drawn by lines L1 to L4 represents a heat pump cycle. Line L1 is ideally parallel with an isentrope 74 and called compression line. Line L2 is called condensation line, line L3 is called expansion line, and line L4 is called evaporation line. Condensation line L2 and evaporation line L4 are determined respectively by a temperature detected by a thermistor provided at the condenser and a temperature detected by a thermistor provided at the evaporator.

[0057] Isothermal lines 71 located in the region on the left side of a saturated liquid line 76 (on the side where the enthalpy is smaller) represent isothermal lines of supercooled liquid. Isothermal lines 72 located in the region surrounded by saturated liquid line 76 and a saturated vapor line 77 represent isothermal lines of wet vapor. Isothermal lines 73 located in the region on the right side of saturated vapor line 77 (on the side where the enthalpy is larger) represent isothermal lines of superheated vapor. Saturated liquid line 76 and saturated vapor line 77 meet at a critical point 75.

[0058] Since compression line L1 is specific to compressor 5, compression line L1 is determined according to the operating state of compressor 5. From the condenser's thermistor detecting the temperature of the condenser (the temperature corresponds to the condensation pressure) and the evaporator's thermistor detecting the temperature of the evaporator (the temperature corresponds to the evaporation pressure), a pressure difference between the inlet and the outlet of the expansion valve is known. Here, essentially the degree of superheat which is used for the conventional control cannot be determined without the evaporator inlet temperature and the evaporator outlet temperature. However, in the case where expansion valve 2 with a certain opening is stable, the pressure difference between the inlet and the outlet of the expansion valve is determined by the compression pressure (the number of revolutions) of compressor 5. Therefore, the degree of superheat (corresponding to Δh1) which is conventionally detected from the evaporator temperature and the evaporator outlet temperature can be calculated from the degree of superheat (corresponding to Δh2) which is determined by means of a thermistor for the discharge temperature (corresponding to temperature sensor 7 in the present embodiment) and a condenser's thermistor (corresponding to temperature sensor 6 or 8 in the present embodiment). For the reason above, in the present embodiment, a target discharge temperature difference (TMP_aim) that provides a target degree of superheat is calculated from the number of revolutions (F) of compressor 5 corresponding to the compression pressure of compressor 5.

TMP_aim=f(F)

[0059] The number of revolutions of compressor 5 may be determined based on a known algorithm. For example, the number of revolutions is determined based on a difference between a room temperature set by operation unit 36 and a current room temperature (temperature sensor 11). Namely, the larger the difference between the set temperature and the room temperature, the greater the number of revolutions of compressor 5.

[0060] Essentially, the degree of superheat can be calculated more reliably by detecting both the temperature of the evaporator inlet and the temperature of the evaporator outlet. The present embodiment, however, chiefly aims to perform control for escaping from an unsafe state (hereinafter referred to as "safety control") as described later herein, rather than accurate calculation of the degree of superheat. Therefore, an experimentally determined pressure difference between the inlet and the outlet of the expansion valve generated by the opening of expansion valve 2 is used to perform control by means of only the temperature difference between the discharge temperature and the condenser temperature (discharge temperature difference).

[0061] Here, while the target discharge temperature difference is determined by calculation, it may also be determined by means of a data table stored in advance in memory 34. Specifically, thermistors (temperature sensors) are provided in advance respectively at the evaporator and the evaporator outlet. Then, the discharge temperature and the condenser temperature when the degree of superheat determined from respective values detected by these thermistors is equal to the target degree of superheat are measured. The difference between the measured discharge temperature and the measured condenser temperature may be used as a target discharge temperature difference corresponding to the number of revolutions of the compressor when they are measured.

[0062] Regarding control of expansion valve 2, for the sake of cycle stabilization immediately after compressor 5 is driven, usually an initial opening of expansion valve 2 is set and the control of the opening based on the discharge temperature difference is not performed for a certain period of time (this period is referred to as mask time). In general, different values of the initial opening may be set respectively for the cooling cycle and the heating cycle as well as the case where the outdoor air temperature is high and the case where the outdoor air temperature is low, to thereby shorten the time taken for stabilizing the cycle.

[0063] After the mask time has elapsed that is a predetermined period of time in which the opening of the expansion valve is set to the initial opening, the opening of expansion valve 2 is controlled so that the opening is equal to the opening determined from the number of revolutions of compressor 5. After this, based on the degree of superheat determined for each number of revolutions of compressor 5, the opening of expansion valve 2 is subjected to PID control (Proportional control, Integral control, Derivative control), so that the discharge temperature difference meets the target discharge temperature difference which is defined for each number of revolutions of compressor 5.

[0064] The PID control is mentioned above as control for making the actual temperature difference closer to a target temperature difference. Here, only the proportional control or only the integral control may be performed. However, it is desirable that control is performed so that the overshoot is reduced as much as possible to thereby make the temperature difference closer to the target temperature difference. It should be noted that the influence of the opening of expansion valve 2 is reflected at a considerably later time on a change of the discharge temperature. Therefore, the opening may be controlled according to a method of the feed-forward control. Specifically, a stable discharge temperature may be predicted from the gradient of the temperature change at the time when the discharge temperature changes due to change of the opening of expansion valve 2. Alternatively, the opening may be controlled by a method according to which a mask time is provided between the time when the opening is changed once and the time when the opening is changed next time. It is desirable that the control method eventually prevents overshoot of the discharge temperature and quickly makes the discharge temperature stable.

[0065] As to safety control:

[0066] The air conditioner in the present embodiment performs safety control in the following manner.

[0067] (1) Safety Control for Preventing Dew Condensation

[0068] Particularly in the cooling cycle operation, the air conditioner in the present embodiment performs control for avoiding the state of dew condensation in the evaporator, namely indoor heat exchanger 3. If the condenser temperature is different by an excessive degree from the discharge temperature, the opening of expansion valve 2 is too small, which causes the state of a small flow of the refrigerant (the state where the refrigerant is likely to be vaporized). Accordingly, the refrigerant quickly becomes dry in indoor heat exchanger 3 (the ratio of the refrigerant that is converted into the gas phase in indoor heat exchanger 3 is high), and thus the refrigerant is separated in indoor heat exchanger 3 into a portion whose heat is exchanged and a portion whose heat is not exchanged. Therefore, a mixture of cold air and warm air is generated which causes the state where dew is likely to be formed in indoor heat exchanger 3.

[0069] In view of the above, the opening of expansion valve 2 is controlled so that the opening is made larger than the opening under normal control (hereinafter referred to as "basic opening") when the discharge temperature difference becomes not less than a threshold value Hth, to thereby prevent dew condensation in indoor heat exchanger 3. Specifically, the opening of expansion valve 2 is controlled so that it is larger by "Shigh" steps than the basic opening under normal control.

[0070] Threshold value Hth will be described with reference to FIG. 8 (http://www.patentsencyclopedia.com/imgfull/20120260678_07). FIG. 8 (http://www.patentsencyclopedia.com/imgfull/20120260678_07) is a diagram showing a relation between a target discharge temperature difference and each threshold value, and the number of revolutions of the compressor. In FIG. 8 (http://www.patentsencyclopedia.com/imgfull/20120260678_07), the vertical axis represents the discharge temperature difference (difference: discharge temperature-(minus) condenser temperature), and the horizontal axis represents the number of revolutions of compressor 5.

[0071] Referring to FIG. 8 (http://www.patentsencyclopedia.com/imgfull/20120260678_07), threshold value Hth is set for example higher by a certain temperature than a target discharge temperature difference line ("TMP_aim" in FIG. 8 (http://www.patentsencyclopedia.com/imgfull/20120260678_07)) which is defined for each number of revolutions of compressor 5. For example, a discharge temperature difference in the state where dew is likely to be formed in the heat exchanger (indoor heat exchanger 3) which is used as an evaporator in the cooling cycle may experimentally be measured in advance. Then, a margin may be provided with respect to the measured discharge temperature difference to determine the temperature difference line of threshold value Hth.

[0072] The number of steps "Shigh" may be determined experimentally or calculated by multiplying the opening of expansion valve 2 that is determined for each frequency (number of revolutions) of compressor 5 by 1/X. It should be noted that even when the same change of the opening is made, a greater number of revolutions of compressor 5 causes a larger change of the temperature, and therefore, it is desirable that the number of correction steps Shigh is larger for a larger number of revolutions of compressor 5.

Shigh (low rev of compressor)<Shigh (high rev of compressor)

[0073] (2) Safety Control for Preventing Liquid Back

[0074] The air conditioner in the present embodiment further performs control for avoiding the state where the refrigerant still in the liquid phase returns to compressor 5 regardless of whether the cycle is the cooling cycle or heating cycle.

[0075] When the discharge temperature difference becomes not more than a threshold value Lth, the opening of expansion valve 2 is controlled so that the opening is smaller than the opening under normal control. Regarding both the cooling cycle and the heating cycle, if the difference between the discharge temperature and the condenser temperature is excessively small, a state is likely to occur where the refrigerant which is still in the liquid phase returns from the heat exchanger used as the evaporator back to compressor 5 (the state of high humidity), which is likely to cause the liquid to return to compressor 5. In such a case, the opening of expansion valve 2 is controlled so that the opening is reduced to a large extent to thereby increase the gas phase of the two phases, namely the gas phase and the liquid phase, after the refrigerant is decompressed. Specifically, the opening of expansion valve 2 is controlled so that the opening is reduced by "Slow" steps relative to the basic opening under normal control. In this way, the lifetime of compressor 5 can be prevented from shortening and compressor 5 can be made less likely to fail.

[0076] Threshold value Lth will be described with reference again to FIG. 8. Referring to FIG. 8 (http://www.patentsencyclopedia.com/imgfull/20120260678_07), threshold value Lth is set, for example, lower by a certain temperature than the target discharge temperature difference line ("TMP_aim" in FIG. 8 (http://www.patentsencyclopedia.com/imgfull/20120260678_07)) which is defined for each number of revolutions of compressor 5. For example, a discharge temperature difference in the state where the liquid back is likely to occur may experimentally be measured in advance. Then, a margin may be provided with respect to the measured discharge temperature difference to determine the temperature difference line of threshold value Hth.

[0077] The number of steps "Slow" here may be determined experimentally or calculated by multiplying the opening of expansion valve 2 which is determined for each frequency (number of revolutions) of compressor 5 by 1/Y. It should be noted that even when the same change of the opening is made, a greater number of revolutions of compressor 5 causes a larger change of the temperature, and therefore, it is desirable that the number of correction steps Slow is larger for a larger number of revolutions of compressor 5.

Slow (low rev of compressor)<Slow (high rev of compressor)

[0078] <Process of Calculating Target Opening of Expansion Valve 2>

[0079] Next, a description will be given of a process of calculating a target opening that is executed by processor 32 for controlling the opening of expansion valve 2 in the present embodiment.

[0080] FIG. 9 is a flowchart showing the process of calculating a target opening in the embodiment of the present invention. This flowchart shows a function by which a target opening of expansion valve 2 is calculated. The process of the flowchart in FIG. 9 is performed periodically for example until an ending event occurs such as an instruction to stop operation. Further, the process shown in the flowchart of FIG. 9 is stored in advance in memory 34 in the form of a program, and processor 32 reads and executes this program to thereby perform the capability of the process of calculating the target opening.

[0081] Referring to FIG. 9, respective values of discharge temperature "TMP_to" and condenser temperature "TMP_con" are first updated (step S1). In the case of the cooling cycle operation, respective temperatures are detected by temperature sensor 7 provided at the outlet of compressor 5 and temperature sensor 6 provided at outdoor heat exchanger 1. In the case of the heating cycle operation, respective temperatures are detected by temperature sensor 7 provided at the outlet of compressor 5 and temperature sensor 8 provided at indoor heat exchanger 3.

[0082] Next, from the temperatures updated in step S1, discharge temperature difference "TMP_diff" is calculated. Specifically, the discharge temperature difference (TMP_diff) is calculated by subtracting the condenser temperature (TMP_con) from the discharge temperature (TMP_to).

[0083] The discharge temperature difference (TMP_diff) is thus calculated, and then the opening (basic opening) of expansion valve 2 under normal control is calculated as an opening implementation value "S" so that the temperature difference (TMP_diff) is identical to the target temperature difference "TMP_aim" (step S3). The target temperature difference (TMP_aim) is set in advance for each frequency of compressor 5 so that a target degree of superheat is met. The formula for calculating the basic opening under normal control may be determined based on the results of experiment performed in advance. Further, such a basic opening (number of steps) may be determined from a data table stored in memory 34, rather than by means of the calculation formula.

[0084] Subsequently, it is determined whether the discharge temperature difference (TMP_diff) is smaller than the set threshold value Hth (step S4). When the discharge temperature difference (TMP_diff) is equal to or larger than threshold value Hth ("FALSE" in step S4), a new opening implementation value S is set to a value determined by adding "S_high" to the basic opening under normal control (opening implementation value S in step S3) so that the opening is further increased (step S5). In this way, the opening implementation value is changed. Processor 32 drives stepper motor 12 using the changed opening implementation value. Consequently, the opening of expansion valve 2 is controlled so that the flow is larger than that under normal control.

[0085] When the discharge temperature difference (TMP_diff) is smaller than threshold value Hth ("TRUE" in step S4), the process proceeds to step S6.

[0086] In step S6, it is determined whether the discharge temperature difference (TMP_diff) is larger than the set threshold value Lth. When the discharge temperature difference (TMP_diff) is equal to or smaller than threshold value Lth ("FALSE" in step S6), a new opening implementation value S is set to a value determined by subtracting "S_low" from the basic opening under normal control (opening implementation value S in step S3) so that the opening is further reduced (step S7). Thus, the opening implementation value is changed. Processor 32 drives stepper motor 12 using the changed opening implementation value. Consequently, the opening of expansion valve 2 is controlled so that the flow is smaller than that under normal control.

[0087] When the discharge temperature difference (TMP_diff) is larger than threshold value Lth ("TRUE" in step S6), the opening implementation value is not changed, and the opening implementation value used for control is set to the basic opening under normal control.

[0088] As seen from the foregoing, according to the present embodiment, only the discharge temperature thermistor (temperature sensor 7) and the thermistor (temperature sensors 6, 8) for the heat exchanger serving as the condenser are used to estimate the degree of superheat. Therefore, the opening of the expansion valve can be controlled without increase of the number of temperature sensors to be used for calculating the degree of superheat. Consequently, the production cost of the air conditioner can be reduced.

[0089] Even in the case where the refrigerant becomes an unstable state, the opening of the expansion valve is immediately controlled so that a safe state is regained, and thus failures of the compressor can be reduced. Consequently, the comfortable and safe air conditioner can be provided.

[0090] It should be construed that embodiments disclosed herein are by way of illustration in all respects, not by way of limitation. It is intended that the scope of the present invention is defined by claims, not by the description above, and encompasses all modifications and variations equivalent in meaning and scope to the claims.

REFERENCE SIGNS LIST

[0091] 1 outdoor heat exchanger; 2 expansion valve; 3 indoor heat exchanger; 4 four-way valve; 5 compressor; 6, 7, 8, 11, 21 temperature sensor; 12 stepper motor; 14 indoor fan; 15 louver; 16 louver motor; 24 outdoor fan; 30 control unit; 32 processor; 34 memory; 36 operation unit; 38 interface unit; 38a recording medium; 100 indoor unit; 200 outdoor unit

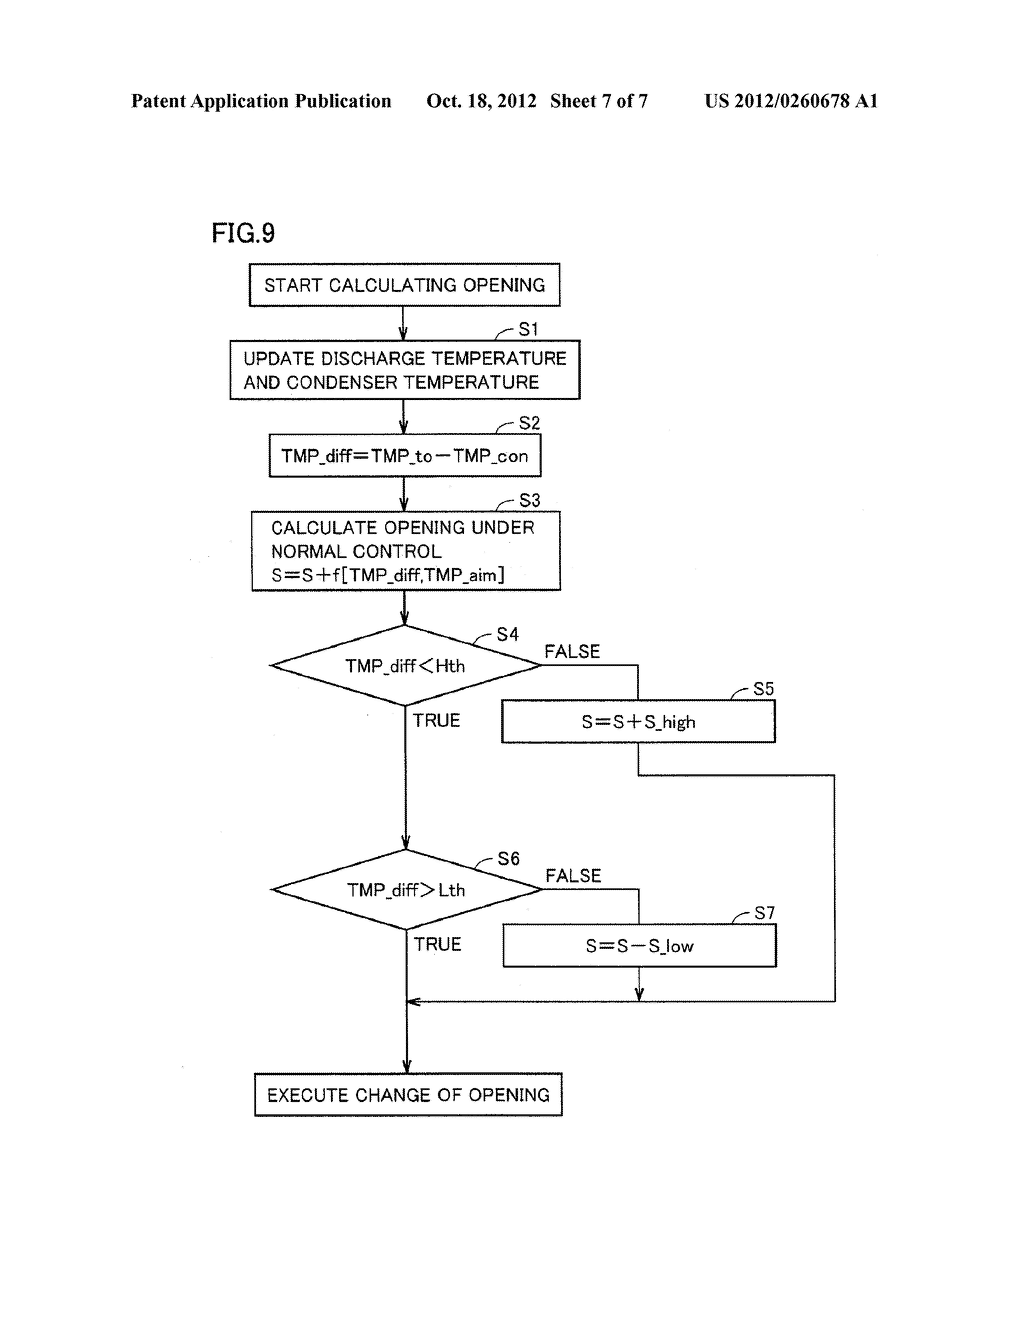
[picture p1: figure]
AIR CONDITIONER, METHOD FOR CONTROLLING OPENING OF EXPANSION VALVE, AND COMPUTER-READABLE RECORDING MEDIUM WITH EXPANSION VALVE OPENING CONTROL PROGRAM RECORDED THEREON - diagram, schematic, and image 08
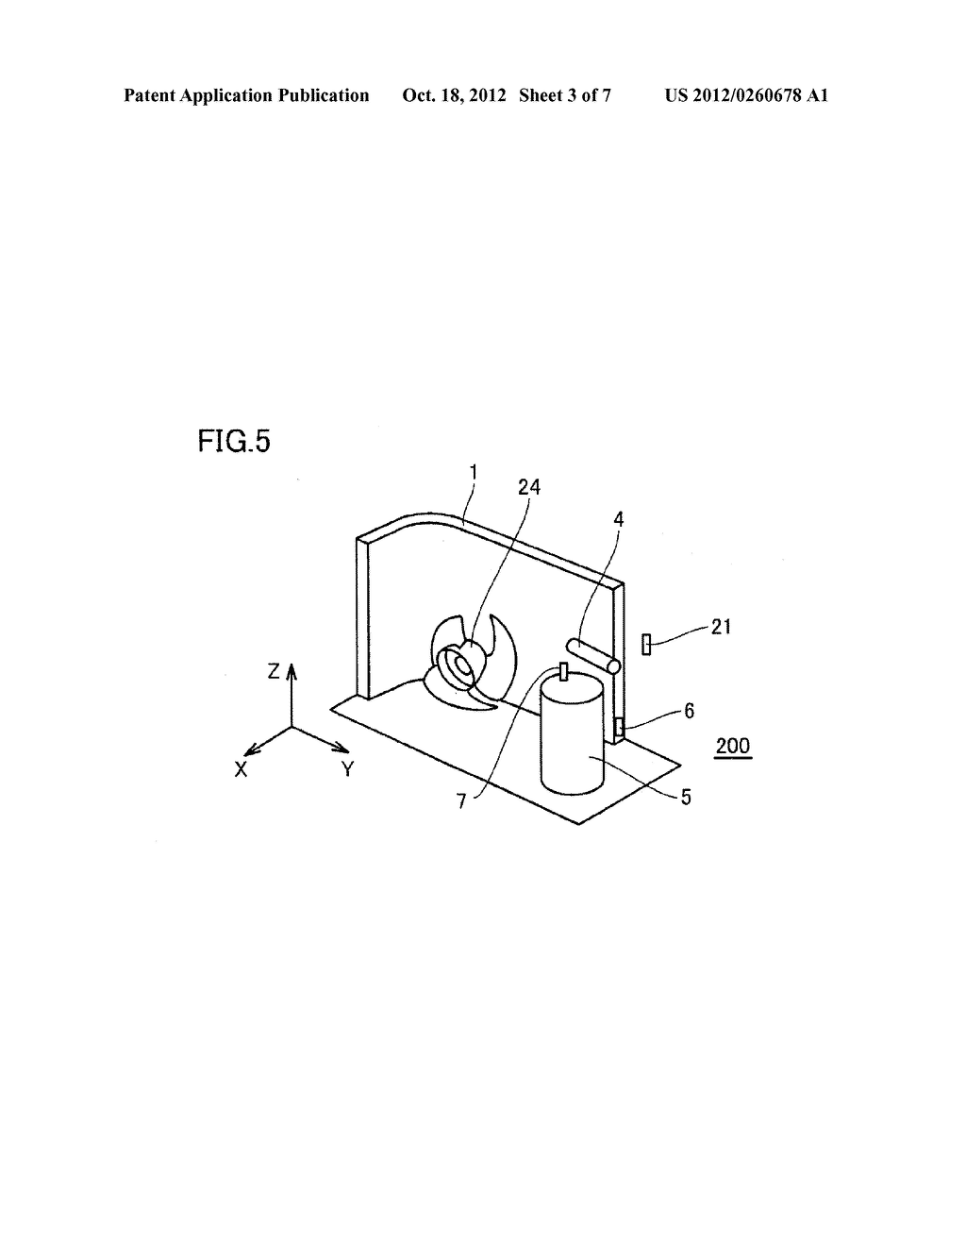
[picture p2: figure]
AIR CONDITIONER, METHOD FOR CONTROLLING OPENING OF EXPANSION VALVE, AND COMPUTER-READABLE RECORDING MEDIUM WITH EXPANSION VALVE OPENING CONTROL PROGRAM RECORDED THEREON - diagram, schematic, and image 04
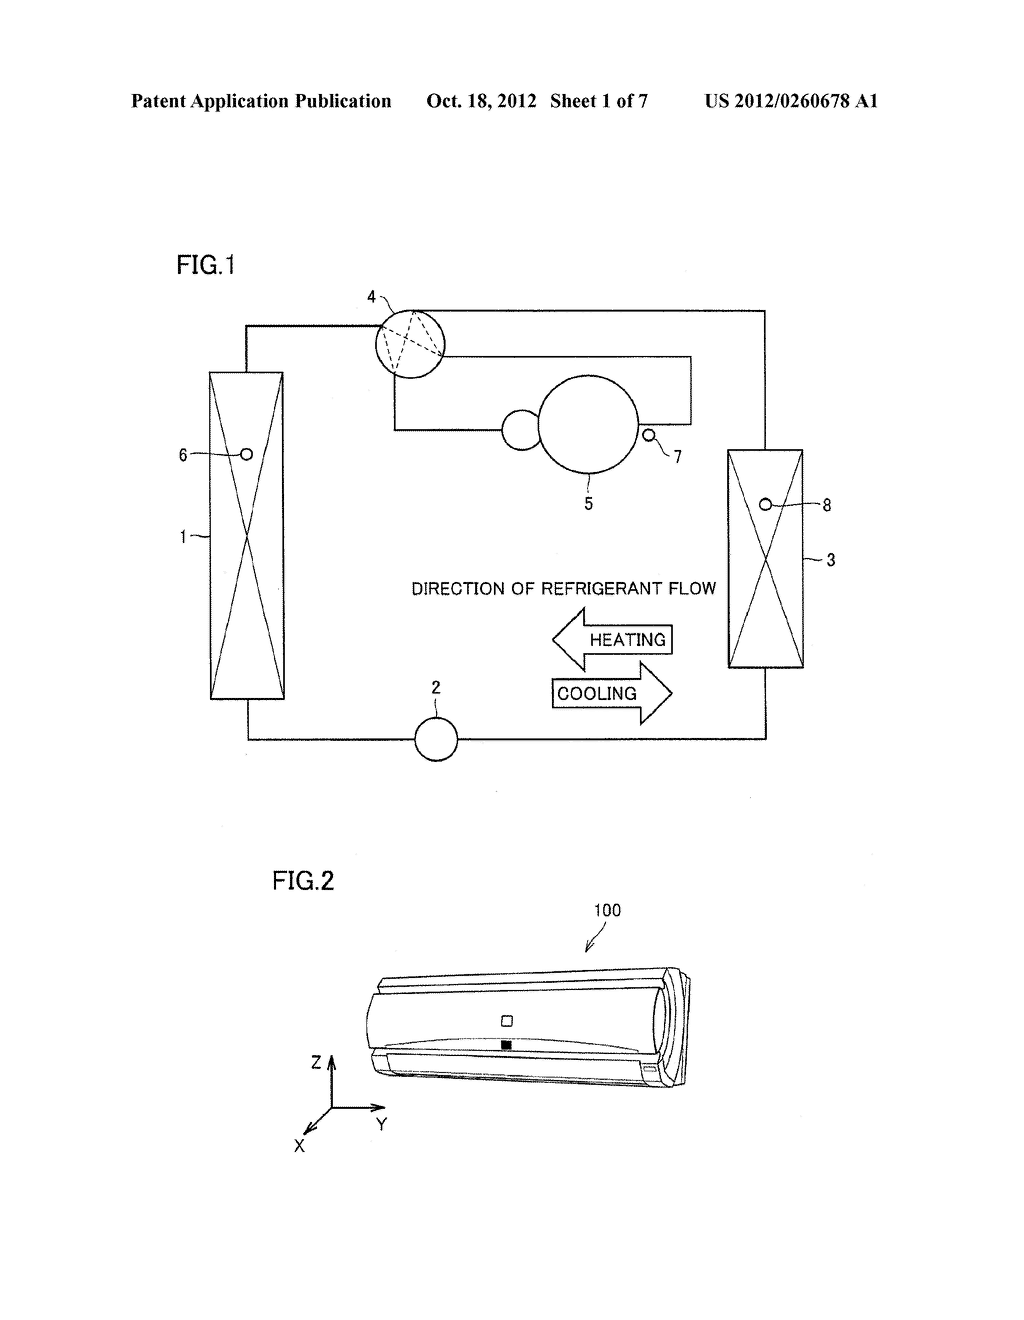
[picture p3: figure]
AIR CONDITIONER, METHOD FOR CONTROLLING OPENING OF EXPANSION VALVE, AND COMPUTER-READABLE RECORDING MEDIUM WITH EXPANSION VALVE OPENING CONTROL PROGRAM RECORDED THEREON - diagram, schematic, and image 02
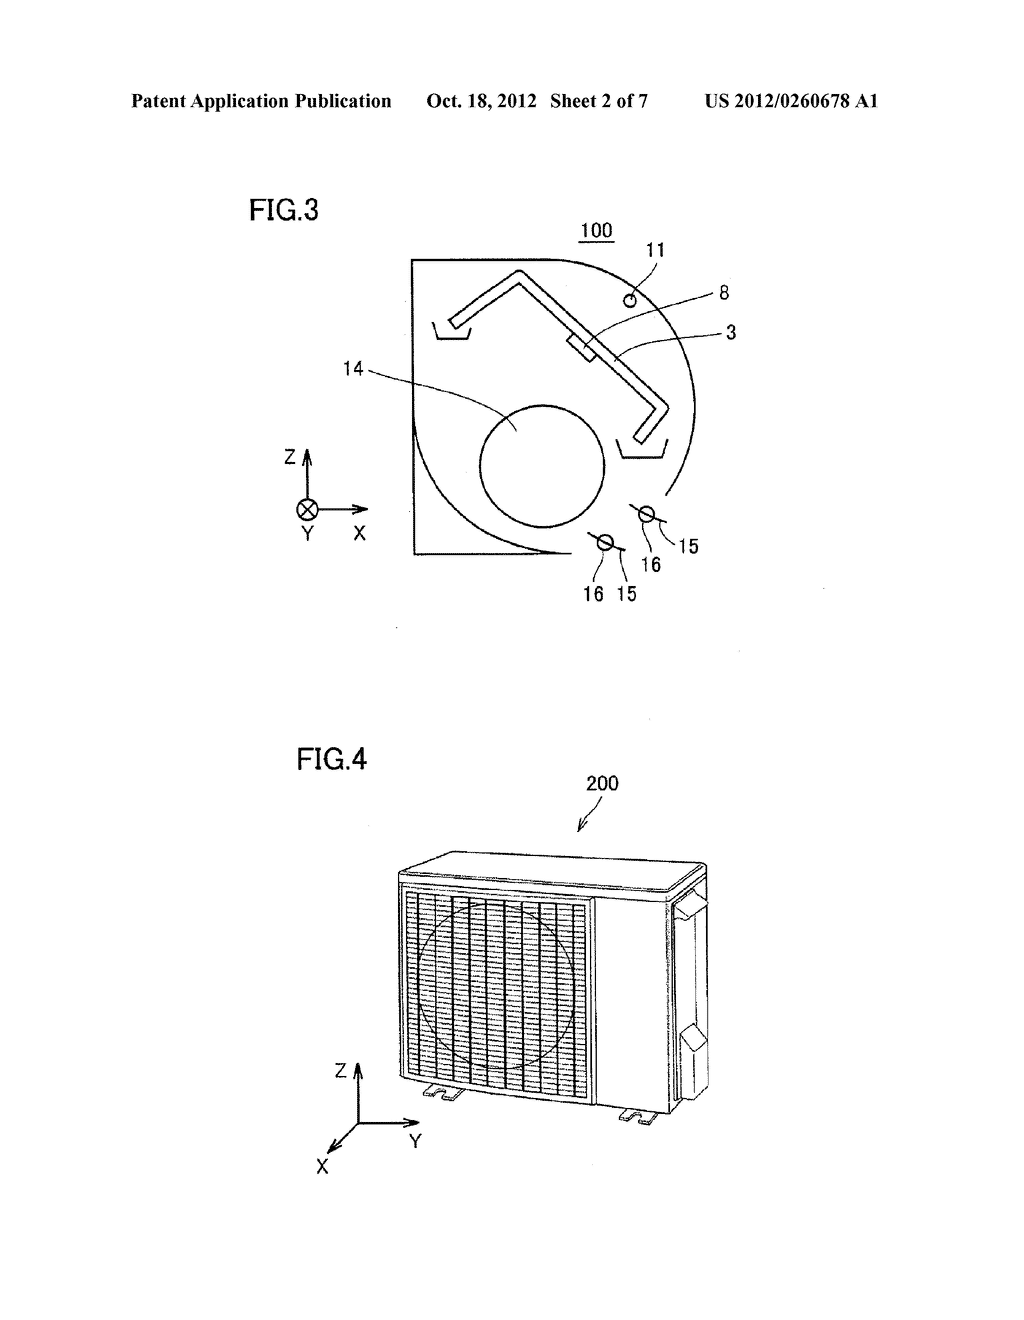
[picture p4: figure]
AIR CONDITIONER, METHOD FOR CONTROLLING OPENING OF EXPANSION VALVE, AND COMPUTER-READABLE RECORDING MEDIUM WITH EXPANSION VALVE OPENING CONTROL PROGRAM RECORDED THEREON - diagram, schematic, and image 03
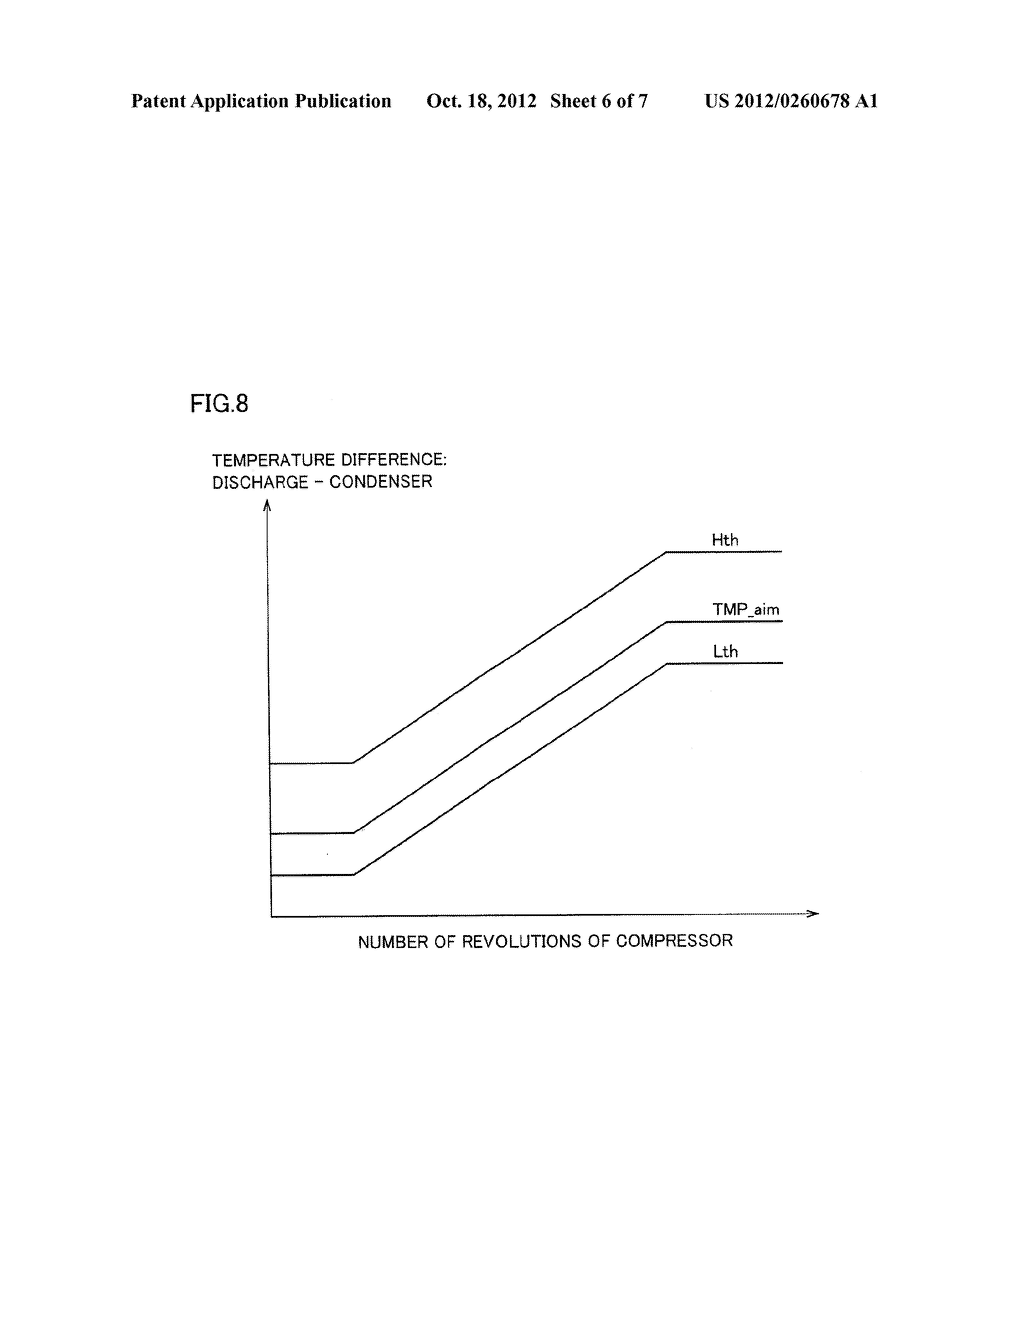
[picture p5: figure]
AIR CONDITIONER, METHOD FOR CONTROLLING OPENING OF EXPANSION VALVE, AND COMPUTER-READABLE RECORDING MEDIUM WITH EXPANSION VALVE OPENING CONTROL PROGRAM RECORDED THEREON - diagram, schematic, and image 07
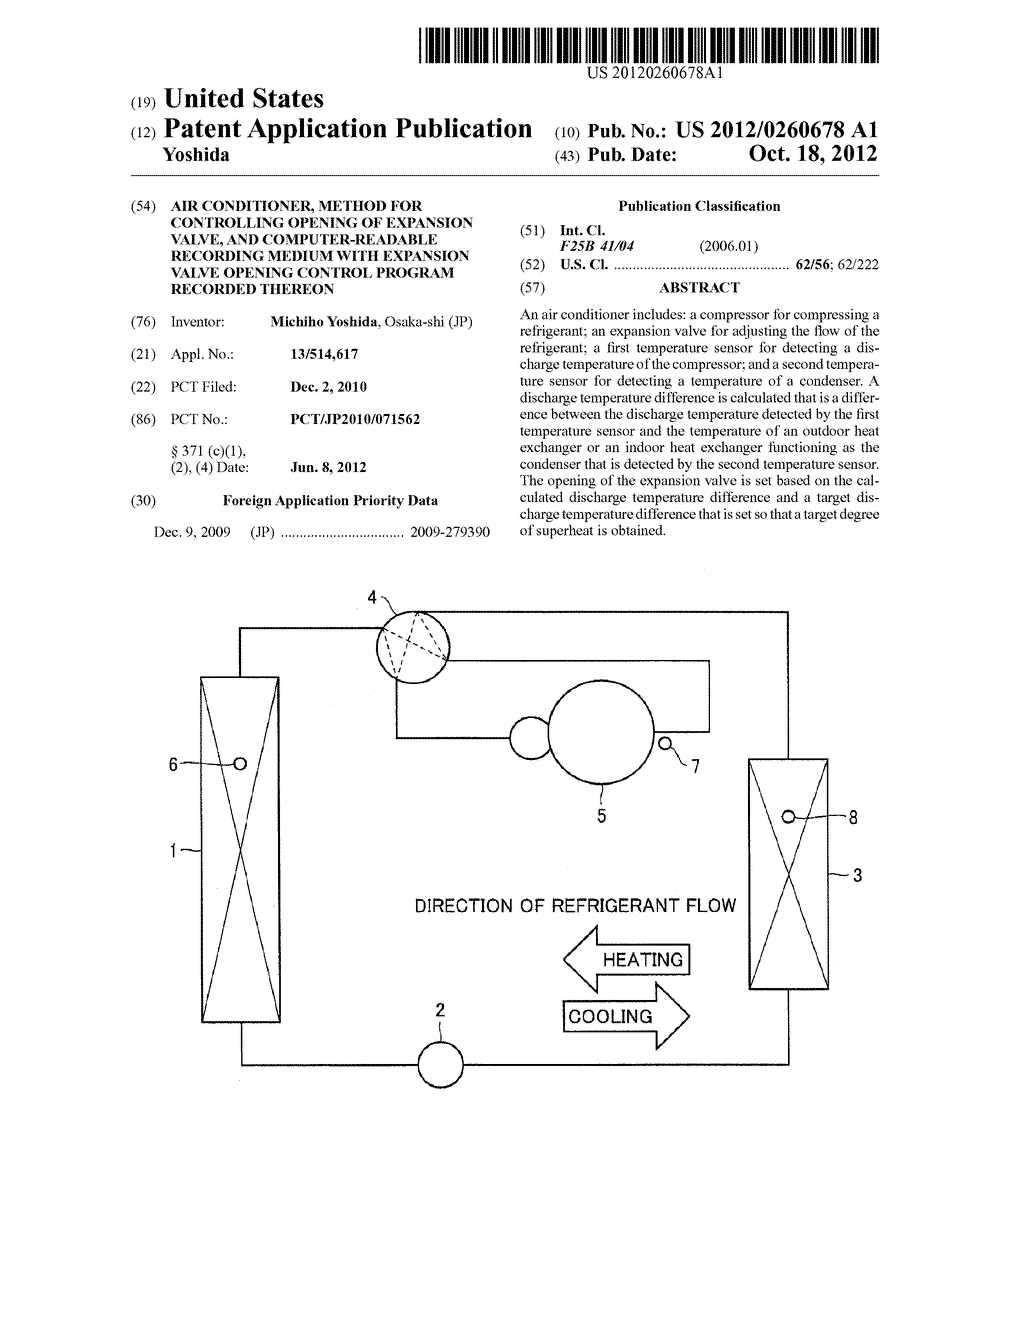
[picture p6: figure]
AIR CONDITIONER, METHOD FOR CONTROLLING OPENING OF EXPANSION VALVE, AND COMPUTER-READABLE RECORDING MEDIUM WITH EXPANSION VALVE OPENING CONTROL PROGRAM RECORDED THEREON - diagram, schematic, and image 01
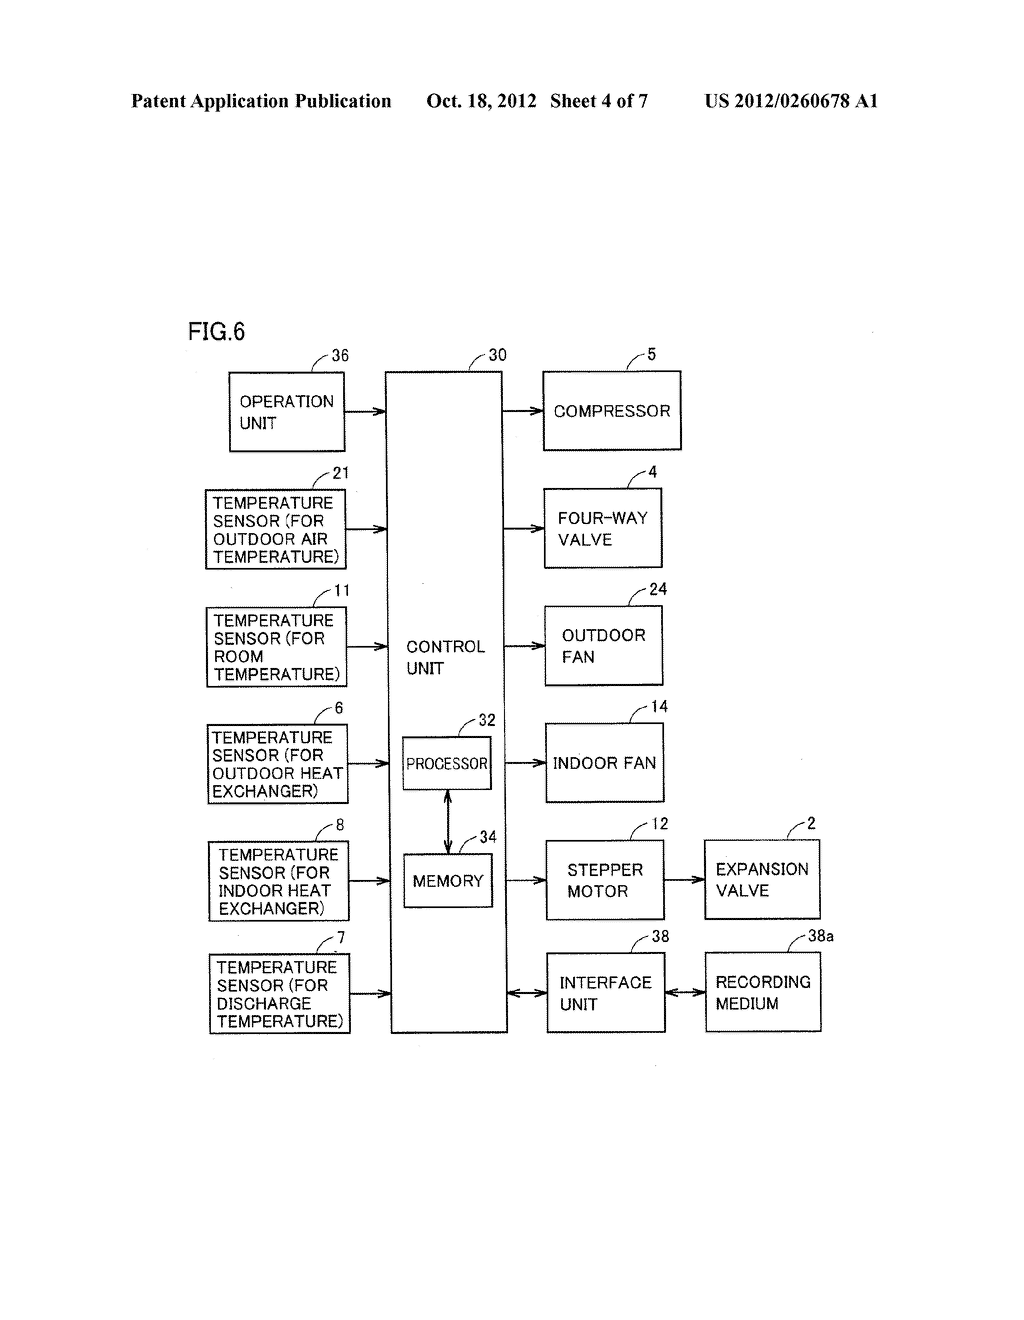
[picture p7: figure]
AIR CONDITIONER, METHOD FOR CONTROLLING OPENING OF EXPANSION VALVE, AND COMPUTER-READABLE RECORDING MEDIUM WITH EXPANSION VALVE OPENING CONTROL PROGRAM RECORDED THEREON - diagram, schematic, and image 05
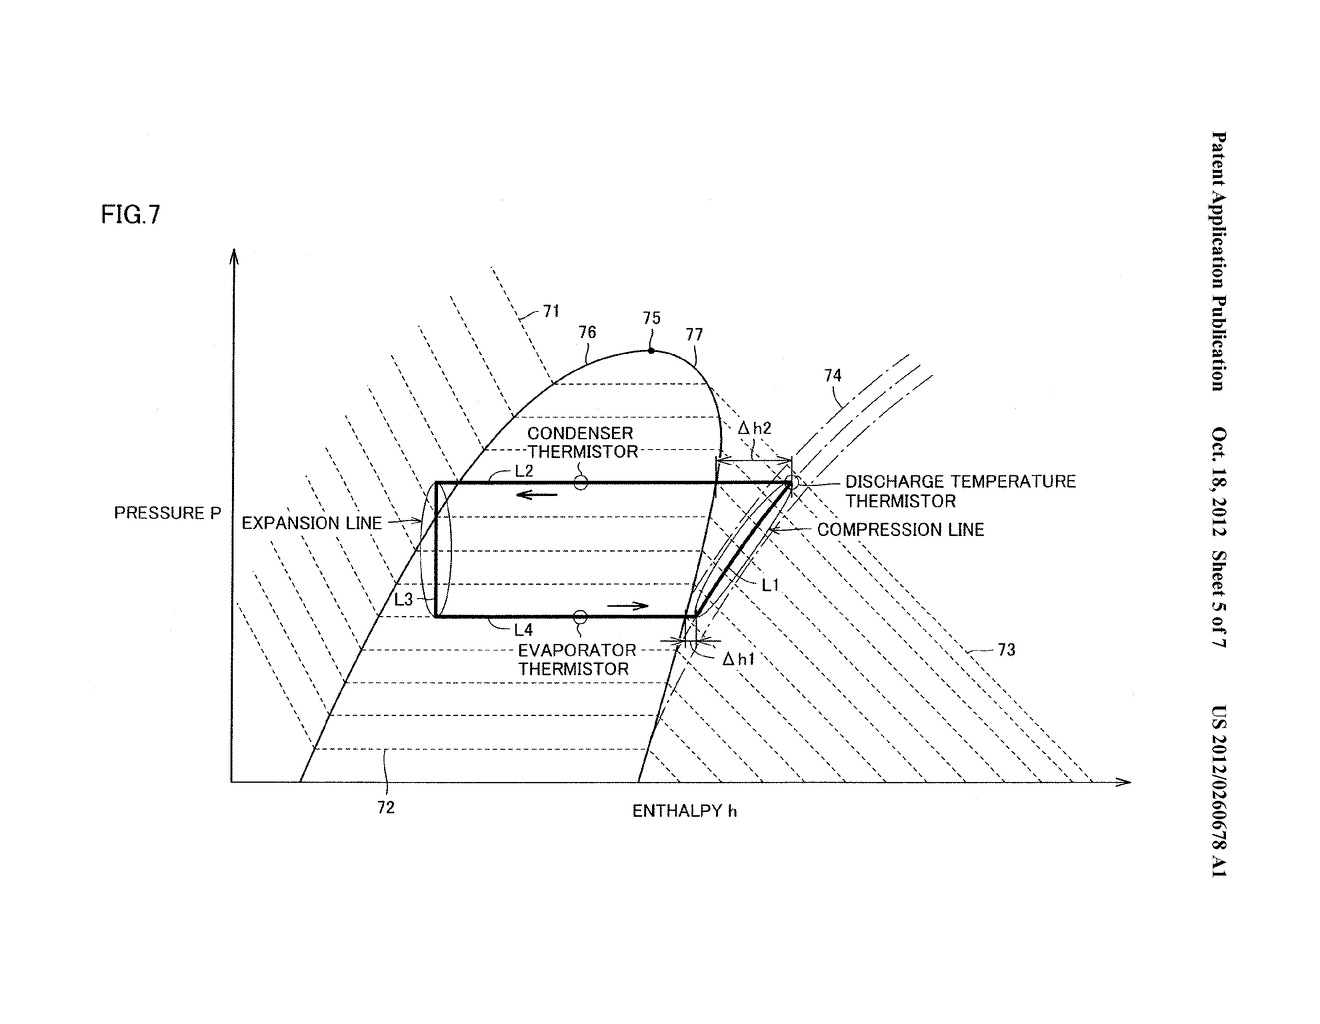
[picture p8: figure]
AIR CONDITIONER, METHOD FOR CONTROLLING OPENING OF EXPANSION VALVE, AND COMPUTER-READABLE RECORDING MEDIUM WITH EXPANSION VALVE OPENING CONTROL PROGRAM RECORDED THEREON - diagram, schematic, and image 06

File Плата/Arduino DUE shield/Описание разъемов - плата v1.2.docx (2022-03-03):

Входы-выходы НК

№: 1 2 3 4 5 6 7 8 9 10

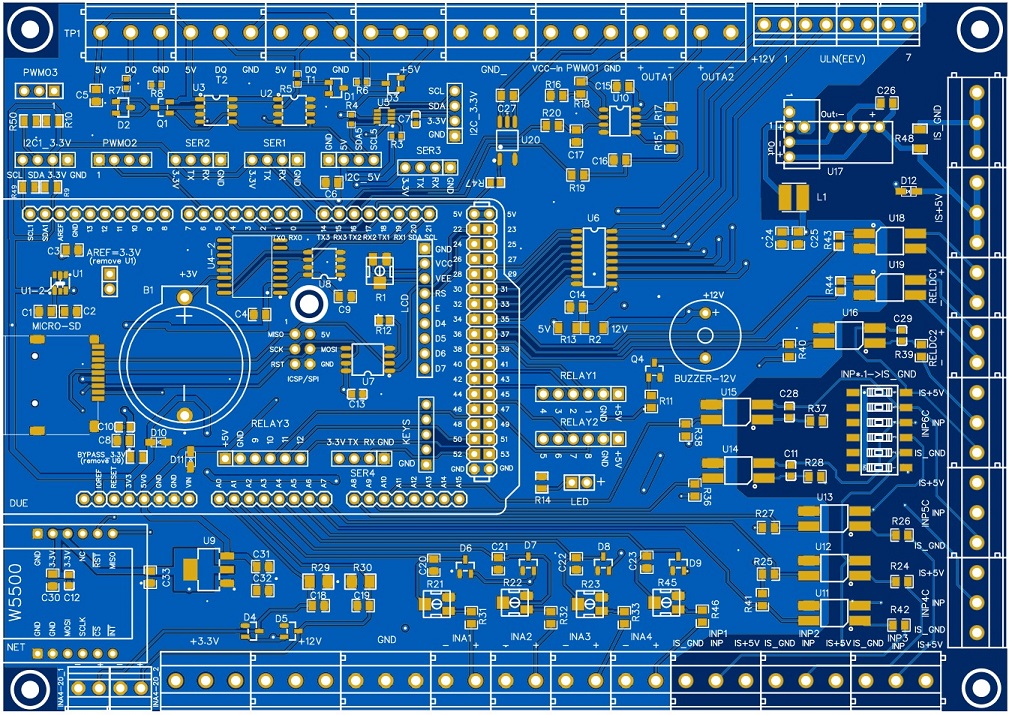
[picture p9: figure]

11

12

13

*

14

MicroSD

15

16

LAN 17

29 28 27 26 25 24 23 22 21 20 19 18

Винтовые разъемы по периметру платы:

1. Датчики температуры DS18B20, двухпроводная или трехпроводная линия (Шина 2)
2. Датчики температуры DS18B20, трехпроводная линия (Шина 1)
3. Датчики температуры DS18B20, трехпроводная линия (Шина 1)
4. Выходы +5V
5. GND (-)
6. Выход изолированный PWM, максимальный ток 8 mA (D5)
7. Выход аналоговый 0-10V (D2)
8. Выход аналоговый 0-10V (D3)
9. ЭРВ (ULN2003), слева на право: +5V или +12V (* - в зависимости от перемычки), D29, D30, D31
10. ЭРВ (ULN2003), слева на право: D32, D33, D34, D35
11. Выход изолированный -5V (GND)
12. Выход изолированный +5V, 1W
13. Реле постоянного тока (оптрон), макс +80V, 50 mA (D36)
14. Реле постоянного тока (оптрон), макс +80V, 50 mA (D37)
15. Вход цифровой изолированный со сглаживающим конденсатором (D38)
16. Вход цифровой изолированный со сглаживающим конденсатором (D64)
17. Вход цифровой изолированный со сглаживающим конденсатором (D63)
18. Вход цифровой изолированный (D62)
19. Вход цифровой изолированный (D61)
20. Вход цифровой изолированный (D60)
21. Вход аналоговый регулируемый R45 (A5/AD2)
22. Вход аналоговый регулируемый R23 (A4/AD3)
23. Вход аналоговый регулируемый R22 (A3/AD4)
24. Вход аналоговый регулируемый R21 (A2/AD5)
25. GND (-)
26. Вход/Выходы +12V
27. Выходы +3.3V
28. Вход аналоговый, токовая петля 4-20 мА, 75 Ом (A1/AD6)
29. Вход аналоговый, токовая петля 4-20 мА, 75 Ом (A0/AD7)

Переключатели INP*.1->IS_GND замыкают выводы IS_GND разъемов №15 - №20 (сверху вниз) на изолированный -5V (GND).

Разъемы на плате:

RELAY1 – Выход на плату реле, 3.3V, контакты 1-4 (D39, D40, D41, D42)

RELAY2 – Выход на плату реле, 3.3V, контакты 5-8 (D44, D45, D46, D47)

RELAY3 – Выход на плату реле, 3.3V, контакты 9-12 (D48, D49, D50, D51)

Платы реле 5V - включение высоким уровнем (High Level Trigger)

KEYS – Кнопки, снизу вверх (GND, D66, D67, D68, D69)

LCD – Цифровой дисплей 20x4 символов, 5V, R1 – регулировка контраста

LED – Зеленый светодиод

SER1 – Порт Serial3, 3.3V

SER2 – Порт Serial2, 3.3V

SER3 – Порт Serial1, 3.3V

SER4 – Порт Serial4, 3.3V

I2C_3.3V – Шина I2C 3.3V (I2C)

I2C_5V – Шина I2C 5V (I2C)

I2C1_3.3V – Вторая шина I2C 3.3V (I2C1)

PWM02 – Выходы/Входы МК 3.3V, 9 мА, доступен PWM (GND, D6, D7, D9)

PWM03 – Выходы/Входы МК 3.3V, 9 мА (D13 – 3 мА), доступен PWM (D11, D12, D13[LED])

B1 – Батарейка CR2032, 3V

Датчики токовая петля 4-20 мА 12V подключаются так:

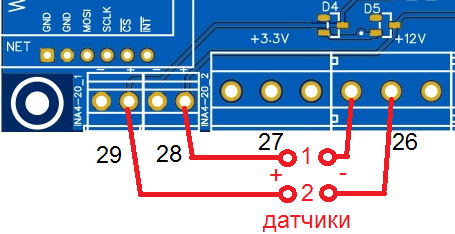
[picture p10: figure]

Доработка китайской платы Arduino DUE R3:

1. Припять резистор поверхностного монтажа (0603 размер) номиналом 10 кОм между ERASE линией и + 3,3В (на ножки транзистора).

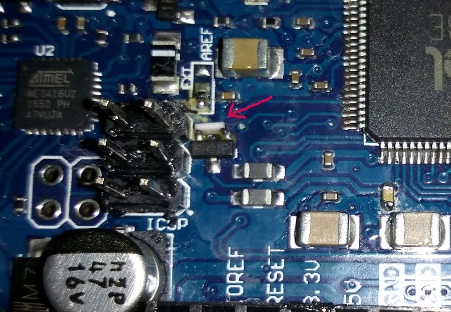
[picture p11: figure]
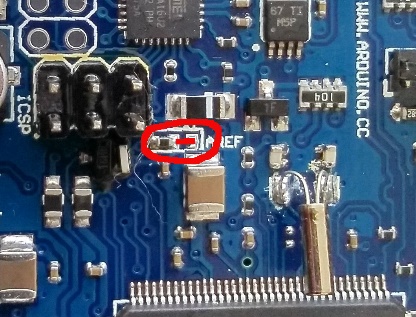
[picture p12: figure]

2. Перепаять перемычку AREF с левых контактов на правые – внешняя опора AREF.

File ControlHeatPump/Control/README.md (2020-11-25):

# ControlHeatPump
Контроллер  теплового насоса

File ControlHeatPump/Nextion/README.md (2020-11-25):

# Nextion
В этой директории лежит все что касается дисплея Nextion. Это не обязательное оборудование!<br>
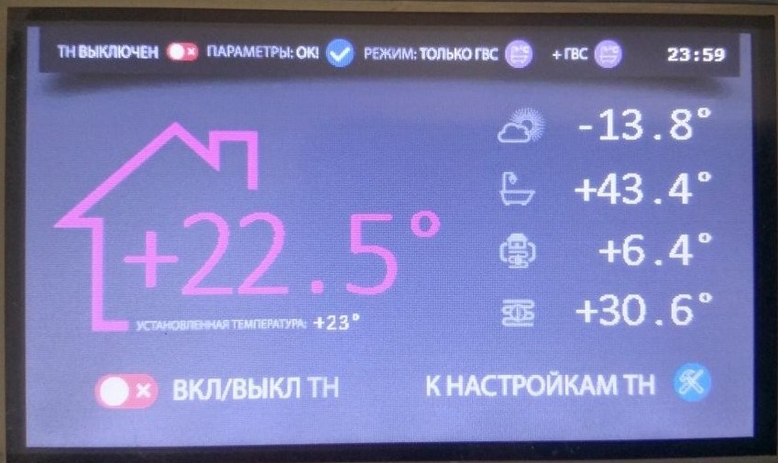
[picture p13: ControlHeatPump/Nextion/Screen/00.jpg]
<br>
Автор данного устройства Sheeny.

Дисплей Nextion используется модель NX4827T043 (https://www.itead.cc/wiki/Product) с
диагональю 4.3 дюйма вот этот : https://www.itead.cc/wiki/NX4827T043 <br>
ОБЯЗАТЕЛЬНО префикс модели NX, с китайским вариантом будут проблемы с редактором.<br>
Цепляется к первому (Serial1) аппаратному порту uart DUE. (ноги D18 D19) (перекрестное соединение
TX-RX). Не смотря на 5 вольтовое питание выходные сигналы с дисплея имеют уровень 3.3 вольта и не
требуют согласования уровней.<br>

Прошивку можно залить через редактор: https://nextion.itead.cc/resources/download/nextion-editor/<br>
или с помощью micro-SD карты: файл nextion.tft нужно переписать на флешку (отформатирована в fat32),
вставить ее в разъем SD на дисплее, включить питание дисплея. Процесс обновления будет отображаться
на дисплее.

Дисплей можно присоеденить по радиоканалу см. файл Nextion+HC-12.pdf.

Файл nextion_800x480.zip - адаптация прошивки для 7 дюймового дисплей Nextion

Проекты делаются в версии Nextion Editor 0.53 не выше, в связи с высокой глючностью
последних версий редакторов.

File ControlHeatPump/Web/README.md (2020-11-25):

# ControlHeatPump
Веб морда для контроллера, необходимо из директории "Main" все файлы записать в корень SD карты или загрузить в SPI Flash (при включенной соответствующей опции в настройках).<br>

Директории:
Main -  основная веб. морда контроллера (может сохраняться на карте и на флеш диске)
mob - вариант мобильной (для телефонов) веб. морды, устаршая версия (частичная работа)
Variant - Варианты замены отдельных файлов основной веб. морды (замена по желанию)

Настройка веб. морды
Необходимо проверить в файле scripts.js - должна быть раскоментирована строка:<br>
var urlcontrol = ''; //  автоопределение (если адрес сервера совпадает с адресом контроллера) <br>
Это вариант если морда лежит на SD карте (ОСНОВНОЙ). <br>
Если морда лежит в другом месте то urlcontrol должно указывать на адрес веб морды.<br>><br>

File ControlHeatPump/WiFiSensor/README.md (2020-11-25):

# WiFi Sensor
ВНИМАНИЕ! Если прошивка не компилится то необходимо заменить буквенное обозначение выводов D2 на просто цифры 2. (причину пока не выяснили, что то с SDK)
В этой директории лежит все что касается WiFi Sensor. Это не обязательное оборудование! <br>
<br>
Автор данного устройства Sheeny.

Удаленное (связь по WiFi) устройство с двумя удаленными датчиками температуры, экраном и web интерфейсом для настроек.
Устройство реализовано на ESP8266. В качестве датчиков используются ds18b20. Экран - OLED 0.96 128x64 по протоколу i2C.

Что умеет устройство:
 - передавать данные с двух датчиков температуры на Народный контроллер
 - выводить данные температуры на экран и web страничку
 - получать параметры от Народного контроллера и выводить их на экран и web страничку
 - сигнализировать экраном об ошибке, возникшей на ТН <br>

Для передачи и получения данных устройство подключается по WIFI к домашней сети.<br>
Если подключиться не удалось, либо "прошитая" сеть не доступна, устройство подымает собственную точку WIFI, подключившись к которой (адрес точки 192.168.4.1) возможно настроить подключение к домашней сети WIFI, либо проверить настройки.
WEB интерфейс позволяет задавать статичный IP для устройства, сканировать эфир на наличие сетей, настраивать параметры подключения к выбранной сети, настраивать параметры собственной точки доступа.
Так же есть возможность настроить параметры подключения к Народному контроллеру.
Можно использовать как 2 датчика температуры вместе, так и один из них. Интервал отправки данных на контроллер так же настраивается.

На экран выводиться следующая информация: <br>
1. Режим работы теплового насоса, которым управляет Народный контроллер
2. Данные с датчика/датчиков температуры
3. Сообщение об отсутствии датчиков температуры. В этом случаи выводится значения TIN и TOUT, полученные с контроллера.
4. Наличие/отсутствие подключения к WIFI и IP адрес, по которому доступен WEB интерфейс устройства.
5. Сигнализация, в случае возникновения ошибки в работе ТН.

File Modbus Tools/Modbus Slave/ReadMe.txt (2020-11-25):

------------------------------------------------------------------------------------
                       Modbus Slave
         Copyright (c) Witte Software. 2002-2017.
------------------------------------------------------------------------------------

Getting started:
-----------------------------
1. Press F3 to setup a connection.
2. Press F8 to setup protocol definition.
   Example:
   You want to simulate 20 holding registers from address 40011 (10).
   - Slave ID  = The ID of your device
   - Function  = 03 Read Holding Registers
   - Address   = 10 (Protocol address)
   - Quantity  = 20

3. To change a value just start typing.

Note: you can always press F1 for help.

Modbus Slave overview:
-----------------------------
Modbus Slave is a powerful, easy to use, slave simulating
tool. Modbus Slave will run on all 32/64-bit Windows versions
in use today - XP, Vista, 7, 8, 8.1 and 10.

You can open up to 32 windows each containing a slave/data
area. A window can simmulate up to 4096 coils or 2048
registers.
OLE Automation for interfacing with Visual Basic
Excel etc. See included example how to edit data with Excel.

Note:
In Windows it is not possible to measure the 3.5 character
idle time between two Modbus frames. That means that it may not
be possible to use Modbus Slave in parallel with another
slave device unless you are sure that the delay in the slave
is > 20ms.

Order information:
--------------------------
Visit http://www.modbustools.com

If not registered you are allowed to use the software
in a 30 days trial period.

Technical Support:
--------------------------
Your feedback is very important for the further development
of Modbus Slave. For bug reports, comments, suggestions or
complaints, please find contact information at
http://www.modbustools.com

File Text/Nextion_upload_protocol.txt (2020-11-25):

NEXTION UPLOAD PROTOCOL (v1.1)
Many customers use the Nextion display in their own business projects. They may need to upload the Nextion firmware through their own MCU. Here we disclose additional considerations to the Upload Protocol beginning with Nextion Editor v0.53 and later.

The Upload Protocol is an advanced technique. Understanding the Upload Protocol is not a requirement if you only upload your firmware through the Nextion Editor.  Version 1.0 of the Upload Protocol can still be used without issues provided:

Addressing Mode is not implemented on the Nextion device
Protocol Reparse is not implemented on the Nextion device
Both Address Mode and Protocol Reparse are advanced techniques and should not be used if not fully understood.  However, additional considerations are needed in the Upload Protocol should either of these advanced techniques be used.

Step 1. Know your Nextion’s serial port

In order to set up a serial connection between Nextion and your MCU, you will first have to find which serial port their Nextion is connected to, and figure out the connection parameters.  Nextion operates at TTL N81, so primarily you are looking for which serial port, and the Nextion’s operating baud rate.

A commonly used technique to locate the Nextion is to send the connect instruction in different connection parameters until a valid connect string is returned.  However, with the introduction of Protocol Reparse and Address Mode in v0.53, newer considerations need to be made.  If Protocol Reparse mode is active, connectÿÿÿ would be interpreted as incoming data, and you would first need to return to passive mode before starting the Upload Protocol.  If Address Mode is active, then Nextion would need to be addressed via its specific address.  Therefore, send the following:

  DRAKJHSUYDGBNCJHGJKSHBDNÿÿÿ
  connectÿÿÿ
  ÿÿconnectÿÿÿ
The first line will cause Nextion to exit active Protocol Reparse and return to passive mode.  The second line is the traditional connect instruction.  The third line is the connect instruction using the broadcast address of 65535.  In this combination, the Nextion will be able to respond with its connect string regardless of which mode it may have been in.

Notes:
1) Conflict resolution with other serial equipment is beyond the scope of describing the protocol.  It is better to create a connection directly using the Nextion’s known parameters than it is to poll in hopes of finding.  2) It is strongly recommended to send an empty instruction (ie: ÿÿÿ) before the connect instruction.  This desired result is gained using the above. 3) Recommended delay to be used between connect attempts is calculated and not random: (1000000/baud rate)+30ms.

Baudrate	2400	4800	9600	19200	38400	57600	115200
Delay(ms)	447	239	135	83	57	48	39

Step 2.  Nextion’s current configuration and address.

Nextion will return a connect string when the right serial port and connection parameters are used.  For example, NX4024T032_011R will return below 8 group’s datas. The data is separated by comma.

comok 1,38024-2556,NX4024T032_011R,99,61488,D264B8204F0E1828,16777216ÿÿÿ
The connect string description:

comok: the handshaking protocol is setup.
1 or 0: Nextion touch abilities: 1 is with touch panel, 0 without touch panel
38024-2556: Partially reserved.  Portion after hyphen is address. 2556 = 0x09FC
NX4024T032_011R: Nextion device model
99: Firmware version S99
61488: MCU code
D264B8204F0E1828: Nextion device serial number
16777216: FLASH Size in bytes

At this point, Protocol Reparse is in passive, but Address Mode may need handling. If Nextion address is 0, then the remainder of the instructions can be sent as normal. But if Nextion is in Address mode where the address is other than 0, then the remainder of the instructions will need to be sent with the two byte address prefixed to each instruction. In the above example connect string, the Nextion address is 2556, or hex 0x09FC. This would require the remaining instructions to be sent prefixed with the two bytes 0xFC 0x09.

The remainder of this document will be presented as if address was 0 and not requiring two byte address prefixing.

Step 3. Conditionally handling sleep and dim

It is best to handle any necessary steps needed to counter sleep functions or low dim at this this point.  If your HMI project does not make use of low dim or sleep functions, you can skip this step and proceed to Step 4.

Using the get instruction, query the necessary system variables for your sleep functions and dim setting used and conditionally adjust them as desired to avoid any potential conflicts with the upload process.  As these are user project dependent and all simple instructions from the Nextion Instruction Set, there is no need to cover in depth here.

Step 4. Upload the firmware

Now that the serial port and current baud rate is known – send the upload command.

whmi-wri filesize,baud,res0ÿÿÿ
filesize: filesize of the tft file (byte)
baud: baud rate
res0: reserved, it can be filled with any ASCII character

The Nextion device will send a 0x05 byte within 500ms after receiving the whmi-wri instruction notifying that it is ready to begin receiving the .tft file contents.  Users must wait until this 0x05 byte is received before sending or risk that the data sent before Nextion was ready will be deemed lost (and therefore a corrupted and unusable upload).  Users must split the .tft file contents into 4096 byte sized packets with the final partial packet size equal to the last remaining bytes (<4096 bytes).

Users then sends out each packet, and in turn wait for the Nextion to return its 0x05 byte confirming reception and readiness to receive the next pack.  Once the final partial packet has been sent and the confirmation 0x05 has been received, the upload portion is complete.

Step 5. After the firmware upload

After the firmware is complete, Nextion will reset and make any necessary firmware adjustments internal to the Nextion device. It is important to wait for these procedures to complete, they are not instant, nor is their time to complete foreknown.  As per the Nextion Instruction Set, Nextion will send an 0x88 Return Data notification indicating it is now ready.  It is wise to wait for such notification before proceeding with your normal upgraded HMI processing.

To make your own upload code, refer to the NexUpload in the Arduino library as an example.

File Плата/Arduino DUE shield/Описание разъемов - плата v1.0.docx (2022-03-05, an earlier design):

Входы-выходы НК

№: 1 2 3 4 5 6 7 8 9 10 11

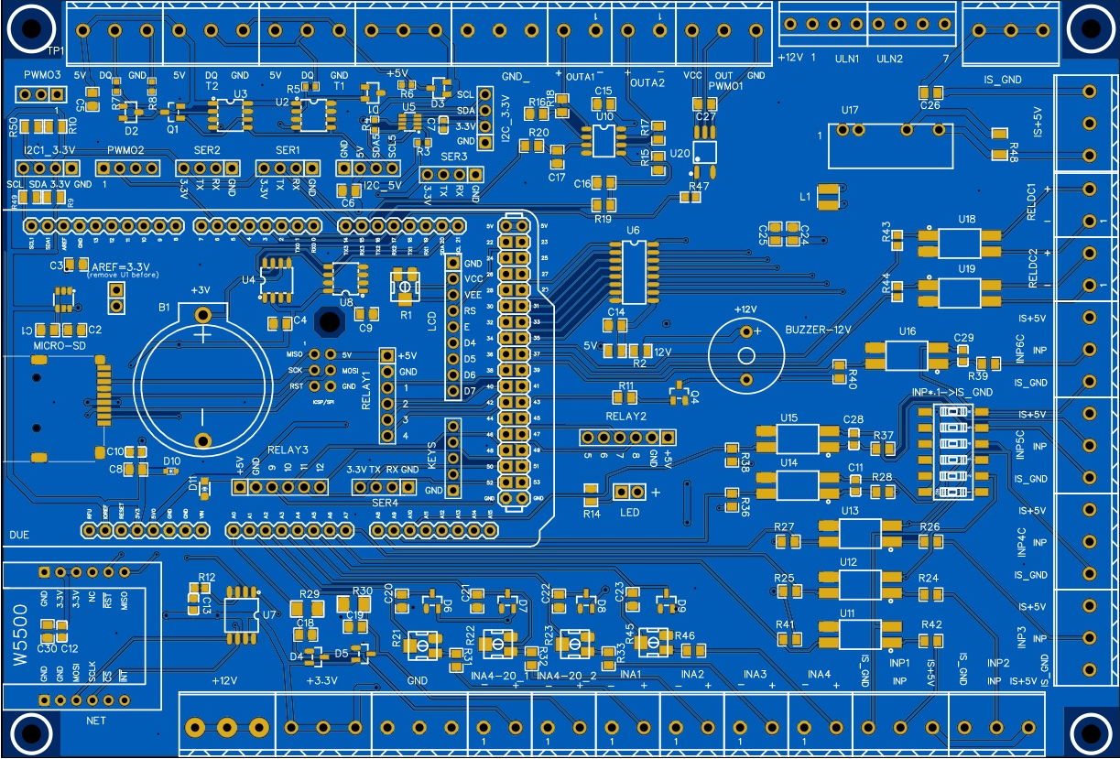
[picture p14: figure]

12

13

14

*

15

MicroSD

16

17

LAN 18

29 28 27 26 25 24 23 22 21 20 19

Винтовые разъемы по периметру платы:

1. Датчики температуры DS18B20, двухпроводная или трехпроводная линия (Шина 2)
2. Датчики температуры DS18B20, трехпроводная линия (Шина 1)
3. Датчики температуры DS18B20, трехпроводная линия (Шина 1)
4. Выходы +5V
5. GND (-)
6. Выход аналоговый 0-10V (D2)
7. Выход аналоговый 0-10V (D3)
8. Выход изолированный PWM, максимальный ток 8 mA (D5)
9. ЭРВ (ULN2003), слева на право: +5V или +12V (* - в зависимости от перемычки), D29, D30, D31
10. ЭРВ (ULN2003), слева на право: D32, D33, D34, D35
11. Выход изолированный -5V (GND)
12. Выход изолированный +5V, 1W
13. Реле постоянного тока (оптрон), макс +80V, 50 mA (D36)
14. Реле постоянного тока (оптрон), макс +80V, 50 mA (D37)
15. Вход цифровой изолированный со сглаживающим конденсатором (D38)
16. Вход цифровой изолированный со сглаживающим конденсатором (D64)
17. Вход цифровой изолированный со сглаживающим конденсатором (D63)
18. Вход цифровой изолированный (D62)
19. Вход цифровой изолированный (D61)
20. Вход цифровой изолированный (D60)
21. Вход аналоговый регулируемый R45 (A5/AD2)
22. Вход аналоговый регулируемый R23 (A4/AD3)
23. Вход аналоговый регулируемый R22 (A3/AD4)
24. Вход аналоговый регулируемый R21 (A2/AD5)
25. Вход аналоговый, токовая петля 4-20 мА, 75 Ом (A1/AD6)
26. Вход аналоговый, токовая петля 4-20 мА, 75 Ом (A0/AD7)
27. GND (-)
28. Выходы +3.3V
29. Вход/Выходы +12V

Переключатели INP*.1->IS_GND замыкают выводы IS_GND разъемов №15 - №20 (сверху вниз) на изолированный -5V (GND).

Разъемы на плате:

RELAY1 – Выход на плату реле, 3.3V, контакты 1-4 (D39, D40, D41, D42)

RELAY2 – Выход на плату реле, 3.3V, контакты 5-8 (D44, D45, D46, D47)

RELAY3 – Выход на плату реле, 3.3V, контакты 9-12 (D48, D49, D50, D51)

Платы реле 5V - включение высоким уровнем (High Level Trigger)

KEYS – Кнопки, снизу вверх (GND, D66, D67, D68, D69)

LCD – Цифровой дисплей 20x4 символов, 5V, R1 – регулировка контраста

LED – Зеленый светодиод

SER1 – Порт Serial3, 3.3V

SER2 – Порт Serial2, 3.3V

SER3 – Порт Serial1, 3.3V

SER4 – Порт Serial4, 3.3V

I2C_3.3V – Шина I2C 3.3V (I2C)

I2C_5V – Шина I2C 5V (I2C)

I2C1_3.3V – Вторая шина I2C 3.3V (I2C1)

PWM02 – Выходы/Входы МК 3.3V, 9 мА, доступен PWM (GND, D6, D7, D9)

PWM03 – Выходы/Входы МК 3.3V, 9 мА (D13 – 3 мА), доступен PWM (D11, D12, D13[LED])

B1 – Батарейка CR2032, 3V

Датчики токовая петля 4-20 мА 12V подключаются так:

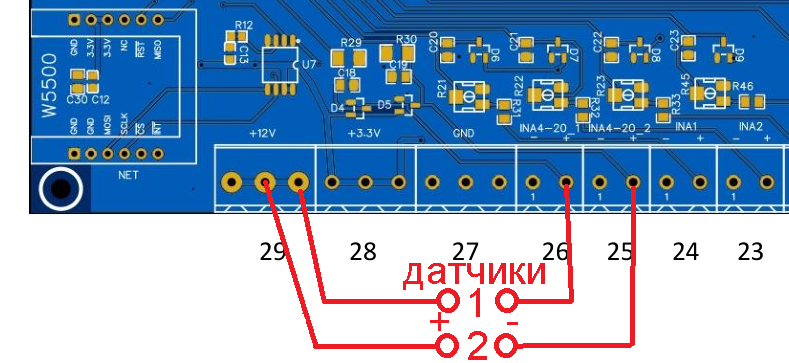
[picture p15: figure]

Доработка китайской платы Arduino DUE R3:

1. Припять резистор поверхностного монтажа (0603 размер) номиналом 10 кОм между ERASE линией и + 3,3В (на ножки транзистора).


2. Перепаять перемычку AREF с левых контактов на правые – внешняя опора AREF.

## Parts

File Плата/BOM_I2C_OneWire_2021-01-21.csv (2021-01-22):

ID | Name | Designator | Footprint | Quantity | Manufacturer Part | Manufacturer | Supplier | Supplier Part | Mounted
1 | DS2482S-100 | U1,U2 | SOIC-8_150MIL | 2 | DS2482S-100+T&R | MAXIM | LCSC | C143306
2 | PCA9306DCTR | U3 | TSSOP8_3 THIN PAD | 1 | ?
3 | I2C (3.3V) | P1 | HDR-4X1/2.54 | 1 | Headers Pins 1*4P | ReliaPro | LCSC | undefined
4 | PCA9306DCUR | U4 | VSSOP-8_2X2.3X05P | 1 | PCA9306DCUR | TI | LCSC | C33196
5 | FM24V10-GTR | U5 | SOIC-8_150MIL | 1 | FM24V10-GTR | RAMTRON | LCSC | C52773
6 | 1.8k | R1,R2 | 0805 | 2 | ? |  |  |  | Yes
7 | 0 | A_1,A_0,A1,A0,AD1,AD_1 | 0603 | 6 | ?
8 | +5V | P2 | HDR-1X1/2.54 | 1 | Header 1*1P | ReliaPro | LCSC | C81276
9 | WJ301V-5.0-2P | P3 | WJ301V-5.00-2P | 1 | WJ301V-5.0-2P | ReliaPro | LCSC | C8475
10 | EK508V-03P | CN1,CN2 | WJ301V-5.00-3P | 2 | EK508V-03P | Dinkle | LCSC | C99393
11 | 300k | R11 | 0805 | 1 | ? |  |  |  | Yes
12 | 100p | C1 | 0805 | 1 | ? |  |  |  | Yes
13 | BSS84LT1G | Q1 | SOT-23(SOT-23-3) | 1 | BSS84LT1G | ON | LCSC | C82079
14 | DS9503P+ | D1,D2 | TSOC-6 | 2 | DS9503P+ | MAXIM | LCSC | C124131
15 | SMBJ6.0A-TR | D4 | SMB(DO-214AA) | 1 | SMBJ6.0A-TR | STMicroelectronics | LCSC | C130396
16 | 2.7k | R3,R4 | 0805 | 2 | ? |  |  |  | Yes

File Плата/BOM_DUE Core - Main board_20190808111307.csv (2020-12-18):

ID | Name | Designator | Footprint | Quantity | Manufacturer Part | Manufacturer | Supplier | Supplier Part | LCSC Assembly | SeeedStudio
1 | W5500 module | NET | W5500_MODULE | 1 | ?
2 | ZS_042/DS3231 | CLK/FRAM | ZS-042 | 1 | DS3231
3 | ADR4530BRZ | REF | SOIC-8_150MIL | 1 | ADR4530BRZ | Analog Devices | LCSC | C208042
4 | 1u | C1 | 0805' | 1 | ?
5 | 0.1u | C2,C3,C4,C5,C9 | 0805' | 5 | ?
6 | Serail1 | SER1,SER2,SER3 | DIP-1X4P-2.54MM RS485-UART | 3 | 210S-1*4P L=11.6MMGold-plated black | Ckmtw | LCSC | C124378
7 | (3.3V) | I2C1,I2C2 | HDR-4X1/2.54 I2C BOARD | 2 | Headers Pins 1*4P | ReliaPro | LCSC
8 | LM1117-3.3 | U1 | SOT-223 | 1 | LM1117IMPX-3.3/NOPB | TI | LCSC | C23984 | Yes
9 | 10u | C6 | 0805' | 1 | ?
10 | LED GREEN | LED1 | LED-1206F | 1 | 15-21/RSC-BS1T2B/2T | Everlight Elec | LCSC | C264385
11 | 330 | R1 | 0805' | 1 | ?
12 | 10к | R2 | 0805' | 1 | ?
13 | 10k | R3,R4,R9,R10 | 0805' | 4 | ?
14 | 10u | C7,C8 | 1206 | 2 | ?
15 | 22.1k | R5,R6 | 0805' | 2 | ?
16 | 9.09k | R7,R8 | 0805' | 2 | ?
17 | KF128_2P_5.08 | VOUT1,VOUT2,IN5V | KF128_2P_5.08 | 3 | KF128L-5.08 | Kefa Electronics
18 | BC817 | Q6 | SOT-23(SOT-23-3) | 1 | BC817 | CJ | LCSC | C8589 | Yes
19 | 100 | R29,R30 | 1206 | 2 | ?
20 | BAT54S | D2,D4,D5,D6,D3 | SOT-23(SOT-23-3) | 5 | BAT54S | SEMTECH | LCSC | C83935 | Yes
21 | 0.01u | C10,C12,C13,C14,C11 | 0805' | 5 | ?
22 | 10K | VR1,VR2,VR3,VR4 | RES-ADJ-SMD_3PIN-V-L3.1-W3.8-H1.62-PITCH1.0 | 4 | EVM3ESX50B14 | PANASONIC | LCSC | C11959
23 | 6.8k | R32,R31,R33 | 0805' | 3 | ?
24 | 0R | R34,R35 | 1206 | 2 | ?
25 | Header-Male-2.54_2x10 | RELAY | HDR-10X2/2.54 | 1 | ? |  | LCSC | C62032
26 | KF301-2P | INA4-20_1,INA4-20_2,INA1,INA2,INA3 | KF128_2P_5.08 | 5 | ? |  | LCSC | C8445
27 | Header-Male-2.54_1x3 | ULN_5-7,REL_8-10,DAC0 | HDR-3X1/2.54 | 3 | Header2.54mm 1*3P | BOOMELE | LCSC | C49257
28 | 0R | J-VOUT-5V | 0805' | 1 | ?
29 | Header-Male-2.54_1x1 | VOUT-PWR | HDR-1X1/2.54 | 1 | Header-Male-2.54_1x1 | ReliaPro | LCSC | C81276
30 | MicroSD board | SD_5V | MICROSD CARD ADAPTER | 1 | ? |  | Hernan
31 | SMBJ5.0A | D1 | SMB/DO-214AA | 1 | SMBJ5.0A | Brightking | LCSC | C78423 | Yes
32 | CC12H2A-TR | U3 | FUSE-CC12H | 1 | CC12H2A-TR | BUSSMANN | LCSC | C340908
33 | Header-Male-2.54_1x2 | 5V | HDR-2X1/2.54 | 1 | 826629-2 | TE Connectivity | LCSC | C86471
34 | MicroSD socket SPI | MICROSD | MICROSD SOCKET | 1 | ?
35 | LCD 1602, 2004. 4-bit mode (HD44780) pin-header | LCD2004 | HDR-16X1/2.54 - LCD1602, LCD2004 | 1 | 16x2 LCD (HD44780)
36 | Arduino Due-Core | DUE | ARDUINO DUE CORE | 1 | ? |  |  | undefined
37 | 2.54mm 1*2P | I2C-2 | HDR-2X1/2.54 | 1 | 2.54mm 1*2P | ReliaPro | LCSC | C36717
38 | Buzzer | BZ | KF350-3.5MM-2P | 1 | WJ2EDGVC-5.08-2P | ReliaPro | LCSC | C8445
39 | Header-Male-2.54_1x5 | KEYS | DIP-1X5P-2.54MM-M | 1 | 210S-1*5P L=11.6MMGold-plated black | Ckmtw | LCSC | C124379
40 | LM358DR | U2 | SOIC-8_150MIL | 1 | LM358DR | TI | LCSC | C5423 |  | 310020021

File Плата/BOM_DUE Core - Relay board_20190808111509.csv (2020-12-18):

ID | Name | Designator | Footprint | Quantity | Manufacturer Part | Manufacturer | Supplier | Supplier Part | _Price | LCSC Assembly | EasyEDA
1 | 330 | R10,R12,R14,R1 | 0805' | 4 | ?
2 | 51 | R11,R13,R15,R17,R2 | 1206 | 5 | ?
3 | MOC3063 | U2,U3,U4,U5,U1 | DIP6 | 5 | ?
4 | BTA16-600CW | Q2,Q3,Q4,Q5,Q1 | TO-220(TO-220-3) | 5 | BTA16-600CWRG | STMicroelectronics | LCSC | C84597
5 | 680 | R16 | 0805' | 1 | ?
6 | G2RL-1-E-5VDC | K1 | G2RL-1-E-CN DC24 | 1 | - | Omron Electronics | LCSC | C231363
7 | SS18 | D1 | SMA(DO-214AC) | 1 | SS18 | MDD | LCSC | C64986 |  | Yes
8 | BC817 | Q7 | SOT-23(SOT-23-3) | 1 | BC817 | CJ | LCSC | C8589 |  | Yes
9 | 10k | R18 | 0805' | 1 | ?
10 | 1k | R19,R20,R4,R5,R7,R9,R22,R24 | 0805' | 8 | ?
11 | FOD852/PC817/TLP126 | U7,U8 | PC817-DIP/SMD | 2 | FOD852SD | ON Semicon | LCSC | C258252 |  | Yes
12 | ULN2003AN | ULN1 | DIP-16_16PIN-LS7.62-L19.69-W6.6-H5.08-PITCH2.54 | 1 | ULN2003AN | TI | LCSC | C90448
13 | Header-Male-2.54_1x8 with numbers | P_REL | HDR-8X1/2.54 | 1 | Header-Male-2.54_1x8 | EasyEDA | EasyEDA | E49256 |  |  | E49256
14 | Header-Male-2.54_2x10 | P1 | HDR-10X2/2.54 | 1 | ? |  | LCSC | C62032
15 | PC817/TLP126/HCPL814 | U9 | PC817-DIP/SMD | 1 | FOD852SD | ON Semicon | LCSC | C258252 |  | Yes
16 | 4.7k | R3,R6,R8,R21,R23,R25,R26 | 0805' | 7 | ?
17 | PC817/TLP126 | U10,U11,U12,U13,U14 | PC817-DIP/SMD | 5 | FOD852SD | ON Semicon | LCSC | C258252 |  | Yes
18 | 0 | OP-12V,OP-5V,R1-5V,R1-12V,U-12V,U-5V | 0805' | 6 | ?
19 | KF128_2P_5.08 | IN12V,IN5V | KF128_2P_5.08 | 2 | KF128L-5.08 | Kefa Electronics
20 | 20k | R27 | 1206 | 1 | ?
21 | 10u | C1,C2,C3,C4 | 1206 | 4 | ?
22 | KF129_2P_5.08 | AC_OUT5,AC_OUT4,AC_OUT3,AC_OUT2,AC_OUT1 | KF129_2P_5.08 | 5 | KF129L-5.08 | Kefa Electronics |  | undefined
23 | Header-Male-2.54_1x3 | ULN-IN_5-7,ULN-OUT_5-7 | HDR-3X1/2.54 | 2 | Header2.54mm 1*3P | BOOMELE | LCSC | C49257
24 | KF129_3P_5.08 | AC_OUT6(R) | KF129_3P_5.08 | 1 | ? | Molex
25 | BTA41 | Q1-2 | TOP3-1 | 1 | BTA41-600BRG | STMicroelectronics | LCSC | C9103
26 | KF350-3P | DC_OUT8(L)/ANALOG_OUT,ULN-OUT | KF350-3P | 2 | WJ2EDGK-5.08-3P-14-00A | ReliaPro | LCSC | C71371
27 | KF350-3.5mm-2p | OP1,OP2,OP3 | KF350-3.5MM-2P | 3 | WJ2EDGVC-5.08-2P | ReliaPro | LCSC | C8445
28 | KF350-3.5mm-2p | DC_OUT7(L),GND,INP1,INP2,INP3,INP4,INP5,INP6 | KF350-2P | 8 | WJ2EDGVC-5.08-2P | ReliaPro | LCSC | C8445
29 | 0.1u | C5 | 1206 | 1 | ?

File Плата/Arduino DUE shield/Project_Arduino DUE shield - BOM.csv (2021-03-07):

ID | Name | Designator | Footprint | Quantity | Manufacturer Part | Manufacturer | Supplier | Supplier Part | Mounted | LCSC Assembly | JLCPCB SMD | Assembly Type | Paste Type
1 | CR2032-BS-2-1 | B1 | BAT-TH_BS-2-1 | 1 | BS-2-1 | Q&J | LCSC | C70376
2 | TMB12A12 | BUZZER-12V | BUZ-TH_BD12.0-P7.60-D0.6-FD | 1 | TMB12A12 | HNDZ | LCSC | C96079 |  | Yes
3 | 10u | C5 | C_805 | 1 | CL21A106KAYNNNE | SAMSUNG | LCSC | C15850 | Yes
4 | 0.1u | C6,C7 | C0603 | 2 | CC0603KRX7R9BB104 | YAGEO | LCSC | C14663 | Yes
5 | 0.1u | C2,C3,C4,C9,C10,C12,C13,C15,C26,C27 | C0603 | 10 | CC0603KRX7R9BB104 | YAGEO | LCSC | C14663
6 | 10u | C1,C8,C14,C16,C17,C24,C25,C30,C31,C32,C33 | C_805 | 11 | CL21A106KAYNNNE | SAMSUNG | LCSC | C15850
7 | 0.01u | C11,C18,C19,C20,C21,C22,C23,C28,C29 | C0603 | 9 | 0603B103K500NT | FH | LCSC | C57112
8 | PACDN042Y3R | D1,D2,D3 | SOT-23-3_L3.0-W1.7-P0.95-LS2.9-BR | 3 | PACDN042Y3R | ON Semicon | LCSC | C233486 |  | Yes
9 | BAT54SLT1G | D4,D5,D6,D7,D8,D9 | SOT-23_L2.9-W1.3-P1.90-LS2.4-BR | 6 | BAT54SLT1G | ON | LCSC | C19726 |  |  | Yes
10 | UCLAMP3301H.TCT | D10 | SOD123-SOD523 | 1 | UCLAMP3301H.TCT | SEMTECH | LCSC | C117558 |  | Yes | Yes | smtWeld | expand
11 | DESD5V0U1BA-7 | D11,D12 | SOD123-SOD523 | 2 | DESD5V0U1BA-7 | Diodes Incorporated | LCSC | C460442
12 | PA_DUE_BRD | DUE | PA_DUE 1 HOLE | 1 | ?
13 | A2541WV-4P | I2C1_3.3V,I2C_3.3V | HDR-TH_4P-P2.54-V I2C 3.3V | 2 | A2541WV-4P | Changjiang Connectors | LCSC | C225479 |  | Yes
14 | A2541WV-4P | I2C_5V | HDR-TH_4P-P2.54-V I2C 5V | 1 | A2541WV-4P | Changjiang Connectors | LCSC | C225479 |  | Yes
15 | KF128L-5.08-2P | INA1,INA2,INA3,INA4,RELDC1,RELDC2 | CONN-TH_P5.08_KF128L-5.08-2P SIGN | 6 | KF128L-5.08-2P | Cixi Kefa Elec | LCSC | C474940 |  | Yes
16 | KF128L-3.5-2P | INA4-20_1,INA4-20_2 | CONN-TH_P3.50_KF128L-3.5-2P SIGN | 2 | KF128L-3.5-2P | Cixi Kefa Elec | LCSC | C474930 |  | Yes |  | manualWeld | expand
17 | KF128L-5.08-3P | INP1,INP2,INP3,INP4C,INP5C,INP6C | CONN-TH_3P-P5.08_KF128L-5.08-3P INP | 6 | KF128L-5.08-3P | Cixi Kefa Elec | LCSC | C474941 |  | Yes
18 | EM-06-Q | INP*.1->IS_GND | SW-SMD_12P-L15.1-W6.0-P2.54-LS9.8 | 1 | EM-06-Q | Diptronics | LCSC | C501580 |  | Yes |  | smtWeld | expand
19 | KF128L-5.08-3P | +3.3V,+5V,+12V,GND,GND_,IS+5V,IS_GND,PWMO1 | CONN-TH_3P-P5.08_KF128L-5.08-3P | 8 | KF128L-5.08-3P | Cixi Kefa Elec | LCSC | C474941 |  | Yes
20 | A2541WV-5P | KEYS | HDR-TH_5P-P2.54-V | 1 | A2541WV-5P | Changjiang Connectors | LCSC | C225480 |  | Yes
21 | 10uH | L1 | IND-SMD_3.0-4.0W | 1 | FNR4018S100MT | cjiang | LCSC | C167808
22 | PZ254V-11-09P | LCD | HDR-TH_9P-P2.54-V-M LCD | 1 | PZ254V-11-09P | XFCN | LCSC | C492408 |  | Yes
23 | TF-01A | MICRO-SD | TF-SMD_TF-01A | 1 | TF-15×15 | SOFNG | LCSC | C111196
24 | W5500 module | NET | W5500_MODULE | 1 | ?
25 | KF128L-5.08-2P | OUTA1,OUTA2 | CONN-TH_P5.08_KF128L-5.08-2P SIGN | 2 | KF128L-3.5-2P | Cixi Kefa Elec | LCSC | C474930 |  | Yes
26 | A2541WV-4P | PWMO2 | HDR-TH_4P-P2.54-V | 1 | A2541WV-4P | Changjiang Connectors | LCSC | C225479 |  | Yes
27 | A2541WV-3P | PWMO3 | HDR-TH_3P-P2.54-V-M | 1 | A2541WV-3P | Changjiang Connectors | LCSC | C225478 |  | Yes
28 | BSS84LT1G | Q1 | SOT-23-3_L2.9-W1.6-P1.90-LS2.8-BR | 1 | LBSS84LT1G | LRC | LCSC | C8492 |  | Yes | Yes
29 | BC817-25LT1G | Q4 | SOT-23-3_L2.9-W1.6-P1.90-LS2.8-BR | 1 | BC817-25LT1G | ON | LCSC | C82635 |  | Yes | Yes
30 | 10K | R1,R21,R22,R23,R45 | RES-ADJ-SMD_3314J | 5 | 3314J-1-103E | BOURNS | LCSC | C36376 |  | Yes
31 | 3.9k | R3,R4 | R0603 | 2 | 0603WAF3901T5E | UniOhm | LCSC | C23018 | Yes
32 | 5 | R5,R6,R7,R8 | R0603 | 4 | 0603WAF510KT5E | UniOhm | LCSC | C25197
33 | 1k | R9,R10,R49,R50 | R0805 | 4 | 0603WAF1001T5E | UniOhm | LCSC | C21190
34 | 10K | R11 | R0603 | 1 | 0603WAF1002T5E | UniOhm | LCSC | C25804
35 | 10k | R15,R16,R19,R20 | R0603 | 4 | 0603WAF1002T5E | UniOhm | LCSC | C25804
36 | 22k | R17,R18 | R0603 | 2 | 0603WAF2202T5E | UniOhm | LCSC | C31850
37 | 75 | R29,R30 | R0805 | 2 | 0805W8F750JT5E | UniOhm | LCSC | C20638
38 | 6.8k | R31,R32,R33,R46 | R0603 | 4 | 0603WAF6801T5E | UniOhm | LCSC | C23212
39 | 4.7k | R25,R27,R36,R38,R40,R41 | R0603 | 6 | 0603WAF4701T5E | UniOhm | LCSC | C23162
40 | 1k | R12,R24,R26,R28,R37,R39,R42,R43,R44 | R0603 | 9 | 0603WAF1001T5E | UniOhm | LCSC | C21190
41 | 330 | R14,R47 | R0603 | 2 | 0603WAF3300T5E | UniOhm | LCSC | C23138
42 | 300 | R48 | R1206 | 1 | 1206W4F3000T5E | UniOhm | LCSC | C17887 |  | Yes | Yes
43 | Header-Male-2.54_1x6 | RELAY1 | HDR-TH_6P-P2.54-V R5V1 | 1 | Header-Male-2.54_1x6 | BOOMELE | LCSC | C37208 |  | Yes
44 | Header-Male-2.54_1x6 | RELAY2 | HDR-TH_6P-P2.54-V R5V2 | 1 | Header-Male-2.54_1x6 | BOOMELE | LCSC | C37208 |  | Yes
45 | Header-Male-2.54_1x6 | RELAY3 | HDR-TH_6P-P2.54-V R5V3 | 1 | Header-Male-2.54_1x6 | BOOMELE | LCSC | C37208 |  | Yes
46 | A2541WV-4P | SER1,SER2,SER3,SER4 | HDR-TH_4P-P2.54-V SERIAL | 4 | A2541WV-4P | Changjiang Connectors | LCSC | C225479 |  | Yes
47 | KF128L-5.08-3P | T1,T2,TP1 | CONN-TH_3P-P5.08_KF128L-5.08-3P DS18B20 | 3 | KF128L-5.08-3P | Cixi Kefa Elec | LCSC | C474941 |  | Yes
48 | REF3030AIDBZR | U1-2 | SOT-23-3_L2.9-W1.6-REF | 1 | REF3030AIDBZR | TI | LCSC | C38423 |  |  | Yes | smtWeld | recommend
49 | DS2482S-100+TR | U2,U3 | SOIC-8_L4.9-W3.9-P1.27-LS6.0-BL | 2 | DS2482S-100+T&R | MAXIM | LCSC | C143306 |  | Yes | Yes
50 | DS3231MZ+ | U4 | SOIC-8_L4.9-W3.9-P1.27-LS6.0-BL | 1 | DS3231MZ+ | MAXIM | LCSC | C107410 |  |  | Yes
51 | MAX3373EEKA+T | U5 | SOT-23-8_L3.0-W1.7-P0.65-LS2.8-TL THIN PADS | 1 | MAX3373EEKA+T | Maxim Integrated | LCSC | C116658 |  | Yes | Yes
52 | ULN2003D1013TR | U6 | SOIC-16_L9.9-W3.9-P1.27-LS6.0-BL | 1 | ULN2003ADR | TI | LCSC | C7512 |  | Yes | Yes
53 | MX25L3206EM2I-12G | U7 | SOIC-8_L5.3-W5.3-P1.27-LS8.0-BL | 1 | MX25L3206EM2I-12G | Micronix | LCSC | C16142 |  | Yes | Yes
54 | M24M01-RMN6TP | U8 | SOIC-8_L4.9-W3.9-P1.27-LS6.0-BL | 1 | M24M01-RMN6TP | STMicroelectronics | LCSC | C79990 |  | Yes | Yes
55 | LM1117MPX-3.3/NOPB | U9 | SOT-223-3_L6.5-W3.4-P2.30-LS7.0-BR | 1 | LM1117IMPX-3.3/NOPB | TI | LCSC | C23984 |  | Yes | Yes | smtWeld | expand
56 | LM358DR2G | U10 | SOIC-8_L5.0-W4.0-P1.27-LS6.0-BL | 1 | LM358DR2G | ON | LCSC | C7950 |  | Yes | Yes
57 | PC817X3NIP1B | U11,U12,U13,U14,U15,U16,U18,U19 | OPTO-SMD-4_L4.6-W6.5-P2.54_SOP-4-L3.9-W4.4 | 8 | EL357N(C)(TA)-G | EVERLIGHT | LCSC | C29981 |  |  | Yes
58 | IF1205S-2W | U17 | PWRM-TH_L11.6-19.6 | 1 | IF1205S-2W | Bothhand Enterprise | LCSC | C494963
59 | TLP104(TPL,E | U20 | SOP-6_5P-L4.4-W3.6-P1.27-LS7.0-BR-PE2 | 1 | TLP104(TPL,E | TOSHIBA | LCSC | C48236 |  | Yes | Yes
60 | KF128L-3.5-2P | ULN(EEV),ULN(EEV)1,ULN(EEV)2,ULN(EEV)3 | CONN-TH_P3.50_KF128L-3.5-2P CORR | 4 | KF128L-3.5-2P | Cixi Kefa Elec | LCSC | C474930 |  | Yes |  | manualWeld | expand

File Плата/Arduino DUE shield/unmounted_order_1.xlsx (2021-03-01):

R2,R13 | 0 | R1206 | Part Number:0 footprint name:R1206 [string length must be less or equal than 1 character] | 2
AREF=3.3V,LED | A2541WV-2P | HDR-TH_P2.54-H-M_A2541WV-2P | 2
PWMO3 | A2541WV-3P | HDR-TH_3P-P2.54-V-M | No part matched | 1
I2C1_3.3V,I2C_3.3V | A2541WV-4P | HDR-TH_4P-P2.54-VI2C3.3V | 2
I2C_5V | A2541WV-4P | HDR-TH_4P-P2.54-VI2C5V | 1
PWMO2 | A2541WV-4P | HDR-TH_4P-P2.54-V | 1
SER1,SER2,SER3,SER4 | A2541WV-4P | HDR-TH_4P-P2.54-VSERIAL | 4
KEYS | A2541WV-5P | HDR-TH_5P-P2.54-V | 1
U1 | ADR3430ARJZ-R7 | SOT-23-6_L2.9-W1.6-P0.95-LS2.8-TL | 1
B1 | CR2032-BS-2-1 | BAT-TH_BS-2-1 | No part matched | 1
D11 | DESD5V0U1BA-7 | SOD-323_L1.8-W1.3-LS2.5-BI | No part matched | 1
RELAY2 | Header-Male-2.54_1x6 | HDR-TH_6P-P2.54-VR5V2 | 1
RELAY3 | Header-Male-2.54_1x6 | HDR-TH_6P-P2.54-VR5V3 | 1
RELAY1 | Header-Male-2.54_1x6 | HDR-TH_6P-P2.54-VR5V1 | 1
U17 | IF1205S-2W | PWRM-TH_IFXXXXS-2W | No part matched | 1
Designator | Name | Footprint | Quantity
DUE | PA_DUE_BRD | PA_DUE1HOLE | No part matched | 1
LCD | PZ254V-11-09P | HDR-TH_9P-P2.54-V-MLCD | 1
MICRO-SD | TF-01A | TF-SMD_TF-01A | No part matched | 1
BUZZER-12V | TMB12A12 | BUZ-TH_BD12.0-P7.60-D0.6-FD | 1
D10 | UCLAMP3301H.TCT | SOD-523_L1.2-W0.8-LS1.6-BI | 1
NET | W5500module | W5500_MODULE | No part matched | 1
INA1,INA2,INA3,INA4,INA4-20_1,INA4-20_2,OUTA1,OUTA2,RELDC1,RELDC2 | WJ500V-5.08-2P-14-00A | CONN-TH_2P-P5.00_WJ500V-5.08-2P-+ | 10
GND_,IS+5V,IS_GND | WJ500V-5.08-3P-14-00A | CONN-TH_3P-P5.00_WJ500V-5.08-3P | 3
+3.3V,+5V,+12V,GND | WJ500V-5.08-3P-14-00A | CONN-TH_3P-P5.00_WJ500V-5.08-3P | 4
T1,T2,TP1 | WJ500V-5.08-3P-14-00A | CONN-TH_3P-P5.00_WJ500V-5.08-3PDS18B20 | 3
PWMO1 | WJ500V-5.08-3P-14-00A | CONN-TH_3P-P5.00_WJ500V-5.08-3PPWMO | 1
INP1,INP2,INP3,INP4C,INP5C,INP6C | WJ500V-5.08-3P-14-00A | CONN-TH_3P-P5.00_WJ500V-5.08-3PINP | 6 | 17
ULN1,ULN2 | XY350V-3.5-4P | CONN-TH_XY350V-3.5-4P | 2 | 2 | 3*2+2*1
верх | 9+6+7+3=25
справа | 10+9=19
низ | 9+12+6=27
12 | 1
10 | 1
9 | 3
6 | 2
7 | 1
3 | 1

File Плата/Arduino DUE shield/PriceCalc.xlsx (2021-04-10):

 | Board Qty | Cost, $
PCB manufacturing | 10 | 320
LCSC parts | 10 | 75
LCSC parts | 10 | 25
Aliexpress parts | 10 | 60
Aliexpress parts (W5500) | 10 | 40
пайка разъемов | 10 | 180
 |  | 700 | 52500

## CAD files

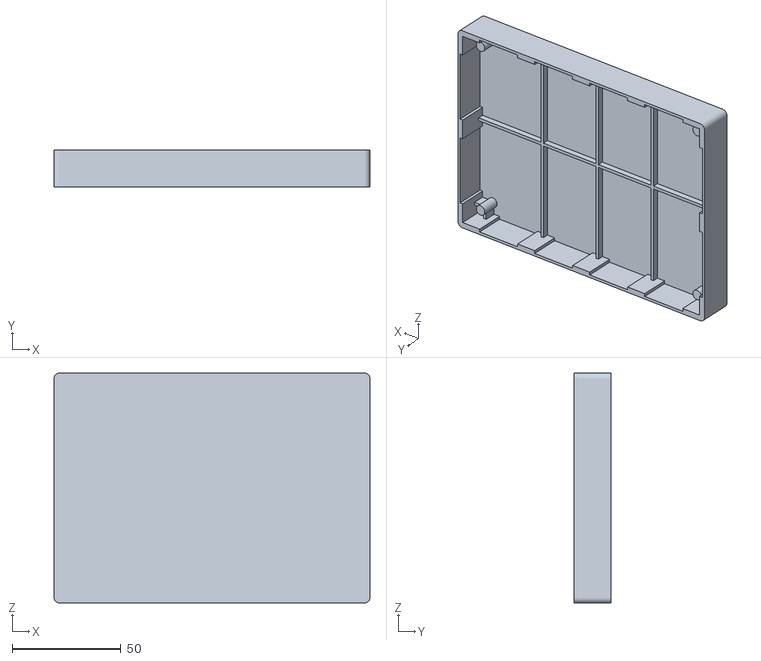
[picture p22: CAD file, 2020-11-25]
ControlHeatPump/Nextion/3D_model/Дно 4.3.stl
145.0 x 17.0 x 105.5

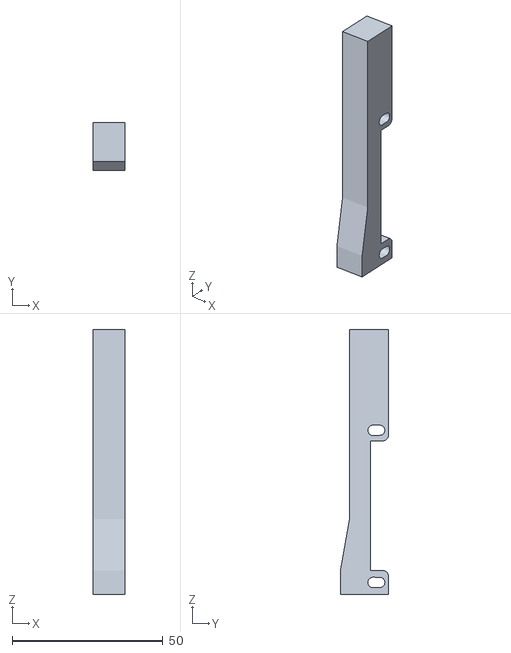
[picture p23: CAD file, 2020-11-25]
Конструктив/Стойка01_ver02.stl
10.5 x 16.0 x 88.0

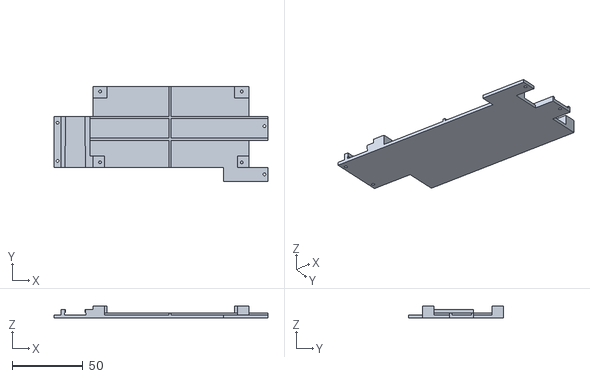
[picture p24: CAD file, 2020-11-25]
Плата/BoardHolder3.stl
151.0 x 67.0 x 8.50

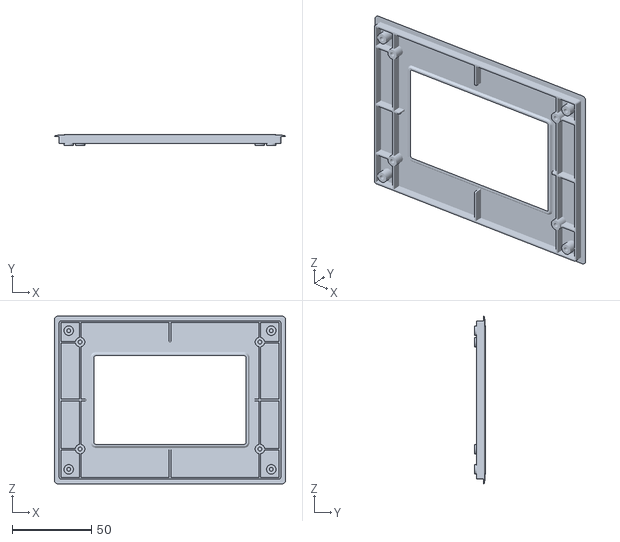
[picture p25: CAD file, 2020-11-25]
ControlHeatPump/Nextion/3D_model/4.3-Bezel.STL
146.0 x 6.80 x 106.0

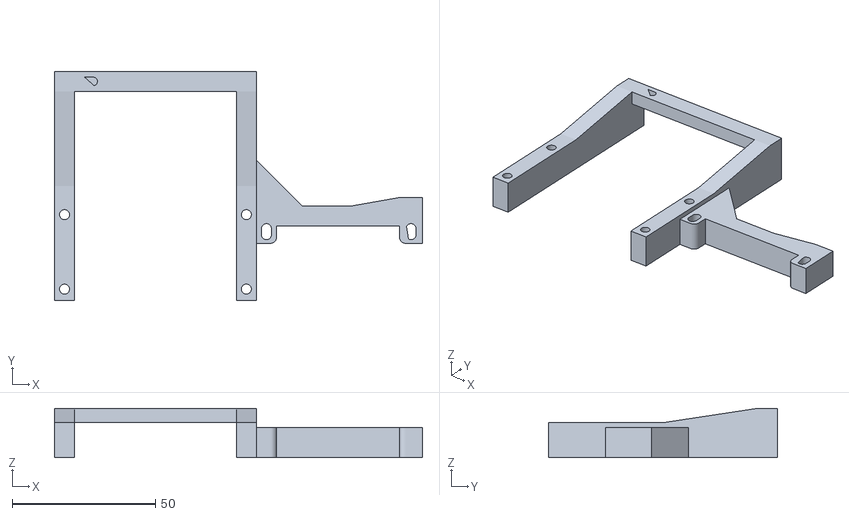
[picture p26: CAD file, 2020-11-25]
Конструктив/Стойка02_ver02.stl
128.5 x 80.0 x 17.2

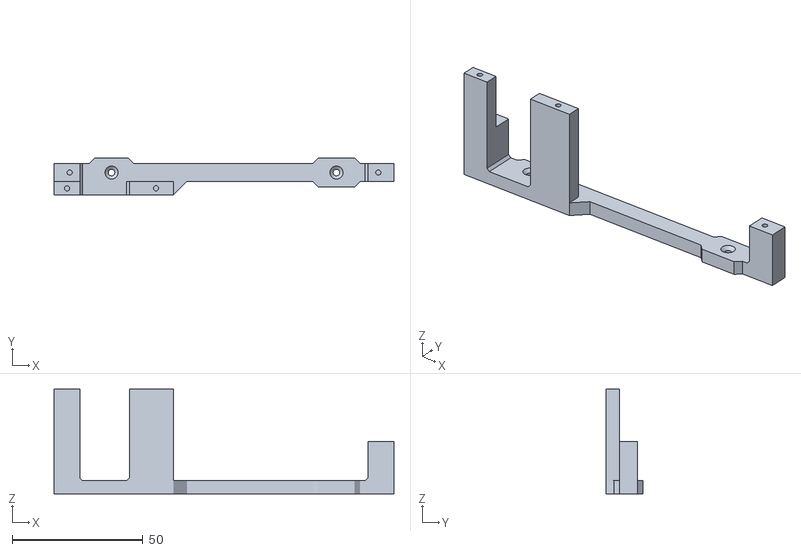
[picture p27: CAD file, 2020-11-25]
Плата/BoardHolder2.stl
130.0 x 14.0 x 40.0

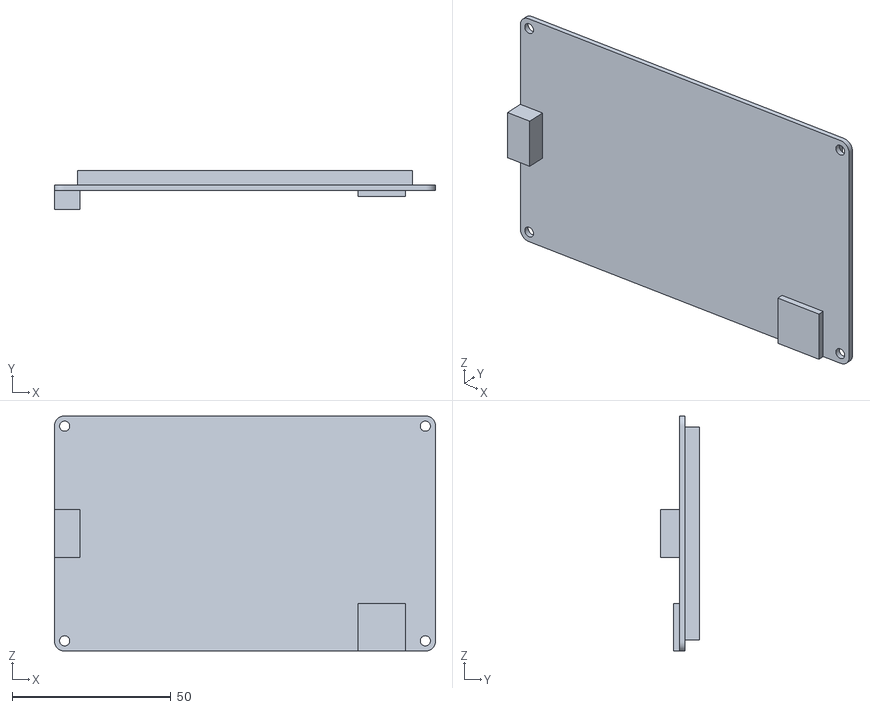
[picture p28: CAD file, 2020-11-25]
ControlHeatPump/Nextion/3D_model/4.3-Display.STL
120.0 x 12.2 x 74.0

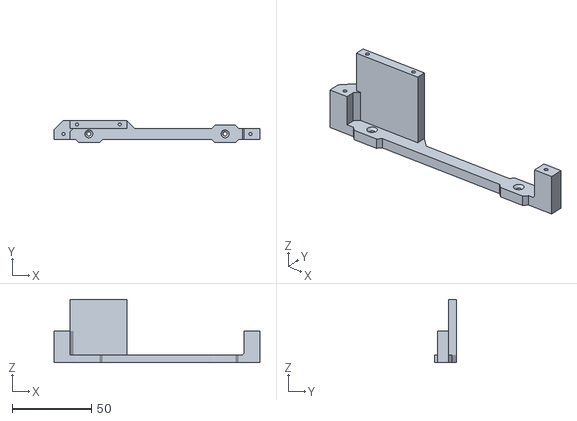
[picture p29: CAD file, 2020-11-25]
Плата/BoardHolder1.stl
130.0 x 14.0 x 40.0

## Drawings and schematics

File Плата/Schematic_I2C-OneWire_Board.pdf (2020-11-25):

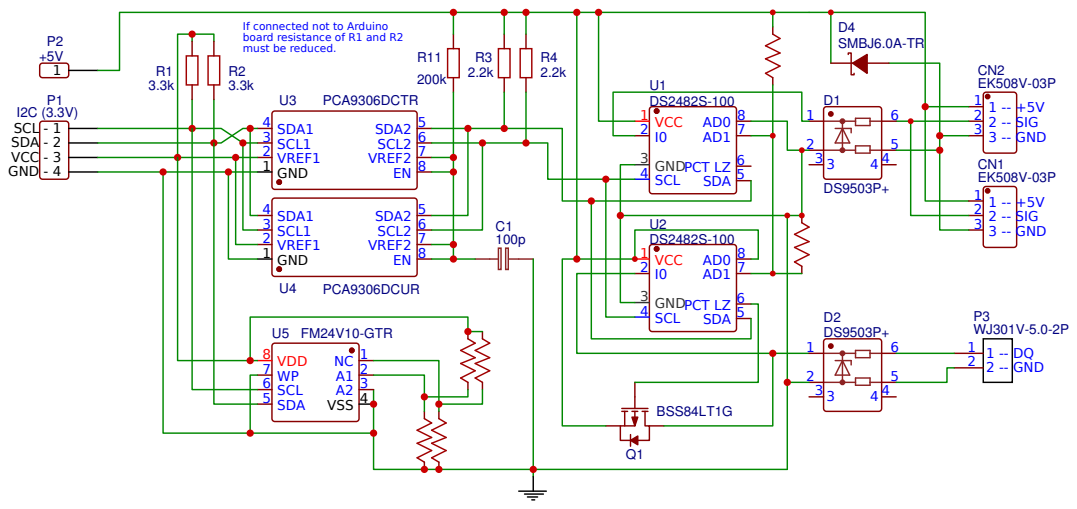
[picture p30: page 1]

If connected not to Arduino
board resistance of R1 and R2
must be reduced.

U5 FM24V10-GTR
VSS 4 SDA 5 SCL 6 WP 7 VDD 8

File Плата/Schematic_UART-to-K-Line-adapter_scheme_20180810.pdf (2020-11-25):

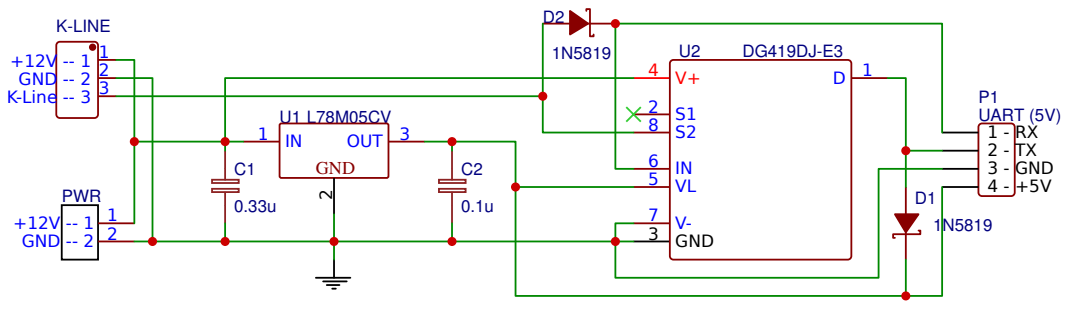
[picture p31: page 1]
TITLE:; UART(5V) to K-Line adapter; REV: 1.0; Date:; Sheet: 1/1; EasyEDA V5.3.2; Drawn By: vad7; UART (5V); 1 - RX 2 - TX 3 - GND 4 - +5V PWR; +12V -- 1 1 GND -- 2 2; K-LINE +12V -- 1 1 GND -- 2 2 K-Line -- 3 3; L78M05CVU1; GND; 2 OUT 3; V- 7 GND 3

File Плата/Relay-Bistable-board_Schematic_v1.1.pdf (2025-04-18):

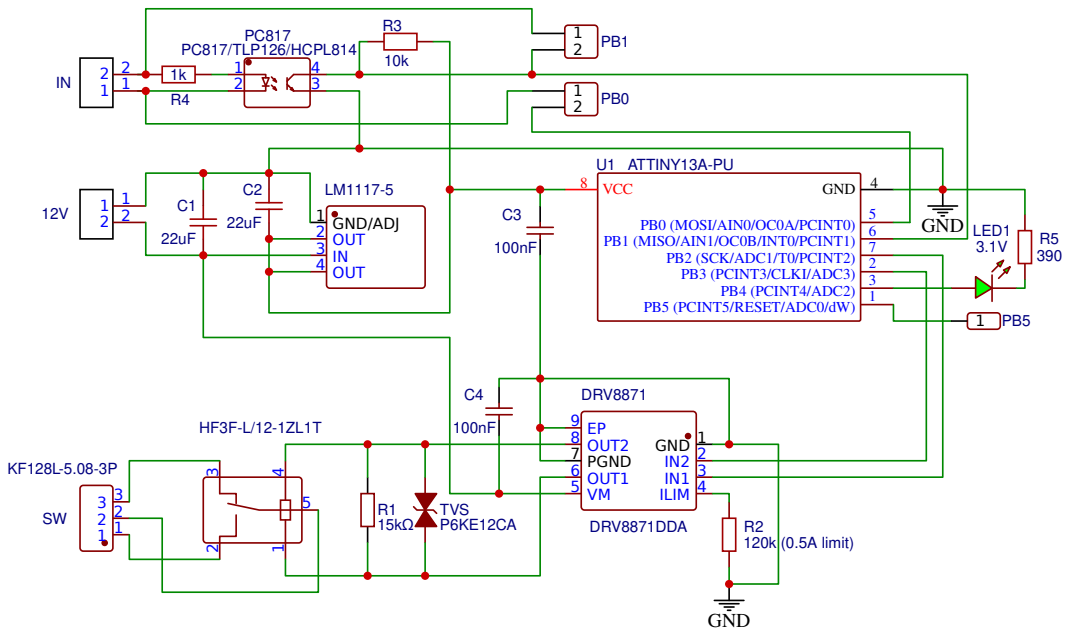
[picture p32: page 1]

DRV8871
ILIM 4 VM 5 OUT1 6 PGND 7 OUT2 8 EP 9

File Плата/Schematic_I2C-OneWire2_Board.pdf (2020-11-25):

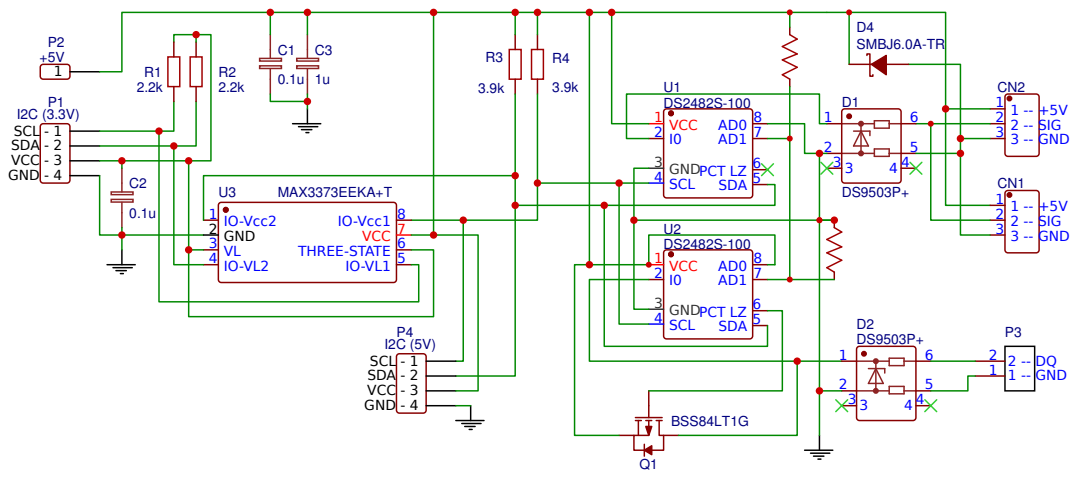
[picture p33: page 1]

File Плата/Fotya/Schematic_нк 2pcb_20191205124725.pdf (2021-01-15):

P1412

P1512

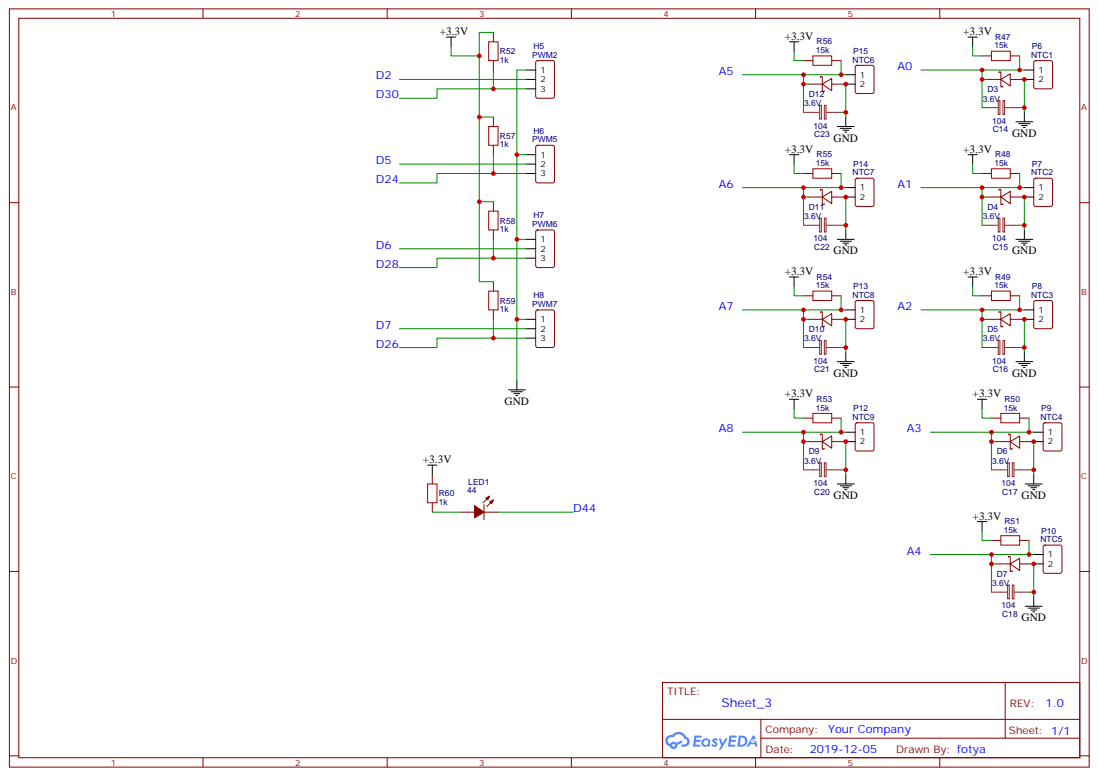
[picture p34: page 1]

P27 1

10987

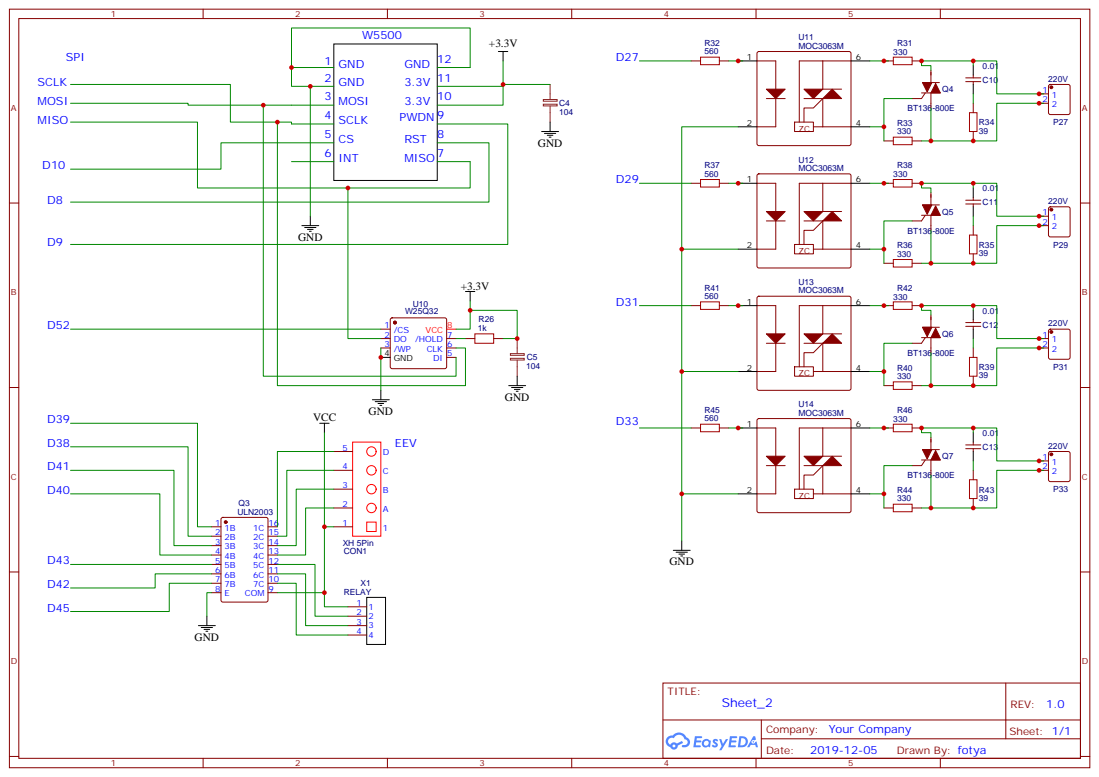
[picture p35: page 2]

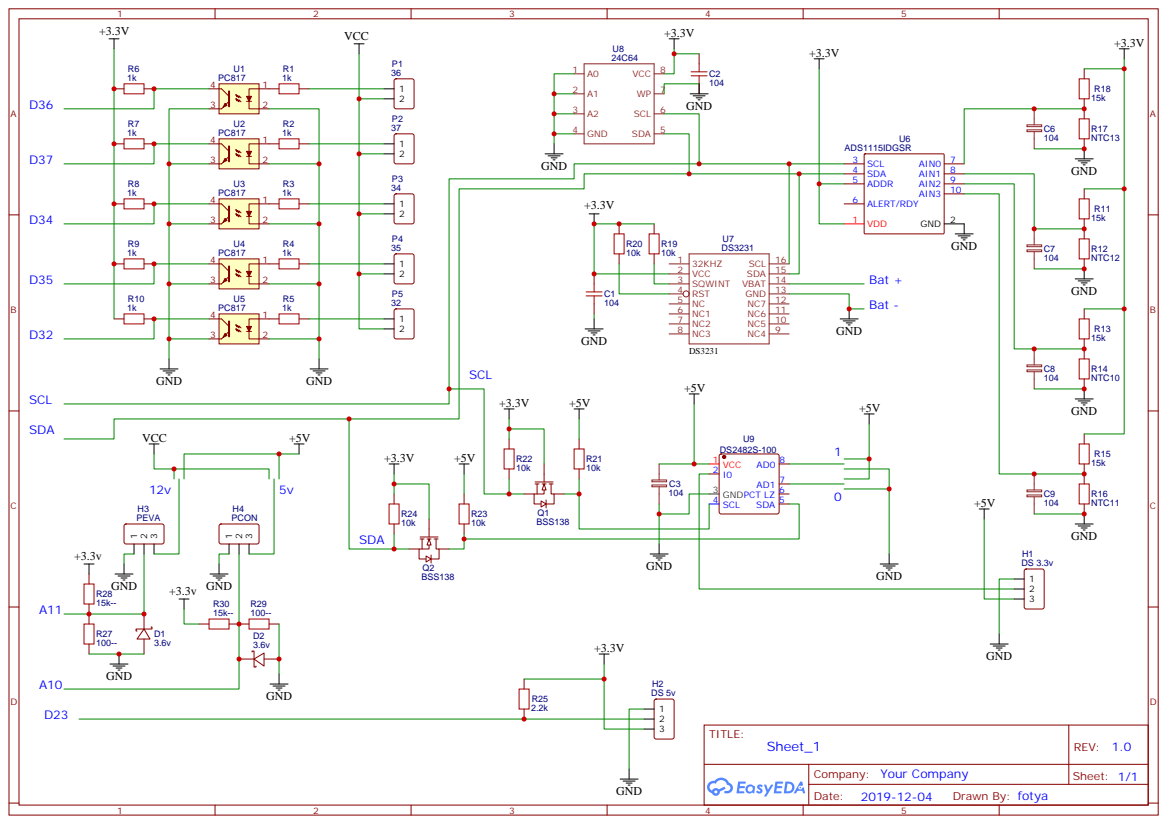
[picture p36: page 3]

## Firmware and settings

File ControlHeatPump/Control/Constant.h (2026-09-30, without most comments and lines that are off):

#define Constant_h
#include "Config.h"                         // Цепляем сразу конфигурацию
#include "Util.h"
#define VERSION			"1.221"				// Версия прошивки
#define VER_SAVE		159					// Версия формата данных в I2C памяти, при изменении добавить размеры структур в HP.Prof.convert_to_new_version() !!!
#define UART_SPEED		115200				// Скорость отладочного порта
#define SerialDbg (*dbgPtr)
Stream* dbgPtr = &Serial;
#define FAST_LIB                            // использование допиленной библиотеки езернета Обычно используется
#define TIME_ZONE         3                 // поправка на часовой пояс по ДЕФОЛТУ
#define NTP_SERVER        "time.nist.gov"   // NTP сервер для синхронизации времени по ДЕФОЛТУ (готовимся к отключению буржуинского инета - "ntp2.stratum2.ru")
#define NTP_SERVER_LEN    60                // максимальная длиная адреса NTP сервера
#define NTP_PORT		  123
#define NTP_LOCAL_PORT    8888              // локальный порт, который будет прослушиваться на предмет UDP-пакетов NTP сервера
#define NTP_REPEAT        3                 // Число попыток запросов NTP сервера
#define NTP_REPEAT_TIME   1000              // (мсек) Время между повторами ntp пакетов
#define PING_SERVER       "192.168.0.1"     // ping сервер по ДЕФОЛТУ
#define WDT_TIME          10                // период Watchdog таймера секунды но не более 16 секунд!!! ЕСЛИ установить 0 то Watchdog будет отключен!!!
#define INDEX_FILE        "index.html"       // стартовый файл по умолчанию для большой морды
#define INDEX_MOB_FILE    INDEX_FILE         // стартовый файл по умолчанию для мобильной морды
#define MOB_PATH          "/mob/"            // Путь к мобильной морде
const char HEADER_BIN[] = "HP-SAVE-DATA";   // Заголовок (начало) файла при сохранении настроек. Необходим для поиска данных в буфере данных при восстановлении из файла
#define MAX_LEN_PM        250               // максимальная длина строкового параметра в запросе (расписание бойлера 175 байт) кодирование описания профиля 40 букв одна буква 6 байт (двойное кодирование)
#define CHART_POINT       300               // Максимальное число точек графика, одна точка это 2 байта * число графиков  //300 - работает
#define ADC_PRESCAL       2					// ADCClock = MCK / ( (PRESCAL+1) * 2 )
#define TARIF_NIGHT_START 23				// Начальный час ночного тарифа электроэнергии
#define TARIF_NIGHT_END   7					// Ночной тариф электроэнергии заканчивается в
#define ON				true
#define OFF				false
#define SEC_1970_TO_2000  946684800UL
byte defaultMAC[] = { 0xDE, 0xA1, 0x1E, 0x01, 0x02, 0x03 };// не менять
const uint16_t  defaultPort=80;
#define GETBIT(b,f)		((b & (1<<(f))) ? true : false)// получить состяние бита
#define SETBIT1(b,f)	(b |= (1<<(f)))		// установка бита в 1
#define SETBIT0(b,f)	(b &= ~(1<<(f)))	// установка бита в 0
#define XBIT(b,f)		(b ^= (1<<(f)))		// инвертировать бит
#define ALIGN(a)		((a + 3) & ~3)
#define SD_REPEAT         3                 // Число попыток чтения карты, открытия файлов, при неудаче переход на работу без карты
#define W5200_THREAD      3                 // Число потоков для сетевого чипа w5200 допустимо 1-4 потока, минимум 2 потока
#define W5200_NUM_PING    2                 // Число попыток пинга до определения потери связи
#define W5200_TIME_PING   500              // мсек Время между попытками пинга (если не удача)
#define W5200_MAX_LEN     2048 //=W5100.SSIZE // Максимальная длина буфера, определяется W5200 не более 2048 байт
#define W5200_NUM_LINK    2                 // Число попыток сброса чипа w5500 и проверки появления связи (кабель воткнут) используется для инициализаци чипа
#define W5200_TIME_LINK   4000              // Максимальное время ожидания устанoвления связи (поднятие Link) кабель воткнут  используется для инициализаци чипа (мсек)
#define W5200_TIME_WAIT   2000              // Время ожидания захвата мютекса (переключение потоков) мсек
#define W5200_TIME_WAIT_MAX (3*60*1000UL)	// Время ожидания захвата макс
#define W5200_SPI_SPEED   SPI_RATE          // ЭТО ДЕЛИТЕЛЬ (SPI_RATE определен в w5100.h)!!! Частота SPI w5200 = 84/W5200_SPI_SPEED т.е. 2-42МГц 3-28МГц 4-21МГц 6-14МГц Диапазон 2-6
#define W5200_SOCK_SYS    (MAX_SOCK_NUM-1)  // Номер системного сокета который не использутся в вебсервере, это последний сокет, НЕ МЕНЯТЬ
#define W5200_RTR         (2*0x07D0)        // время таймаута в 100 мкс интервалах  (по умолчанию 200ms(100us X 2000(0x07D0))) актуально для комманд CONNECT, DISCON, CLOSE, SEND, SEND_MAC, SEND_KEEP
#define W5200_RCR         (0x04)            // число повторов передачи  (по умолчанию 0x08 раз))
#define MAIN_WEB_TASK     0                 // какой поток вебсервера является основным (поток в котором идет отправка MQTT и уведомлений) обычно 0
#define WEB_MAX_LOCK_TIME 10000UL			// максимальное время не выполенния web_server() для сброса семафора, мсек
#define DISK_TIME_WAIT		1000			// Время ожидания семафора SD/Flash
#define NEXTION_PORT         Serial1        // Аппаратный порт куда прицеплен дисплей
#define NEXTION_PORT_SPEED   9600           // Скорость порта, бод
#define NEXTION_UPDATE       5000           // Время обновления информации на дисплее Nextion (мсек)
#define NEXTION_BOOT_TIME    300            // Время для загрузки дисплея, если при сбросе дисплей не находится надо увеличить (мсек)
#define NEXTION_READ         50             // Время опроса дисплея Nextion (мсек) разбор входной очереди
#ifdef LCD2004
#undef KEY_ON_OFF
#define LCD_COLS				20			// Колонок на LCD экране
#define LCD_ROWS				4			// Строк на LCD экране
#define DISPLAY_UPDATE			2000           // Время обновления информации на дисплее (мсек)
#define KEY_CHECK_PERIOD		5              // ms
#define KEY_DEBOUNCE_TIME		50             // ms
#define DISPLAY_SETUP_TIMEOUT	600000         // ms
#define LCD_SetupFlag 			0x80000000
#define LCD_SetupMenuItems		6
#define LCD_MainScreenMaxItem	3				// 0..
#define LCD_SetupMenu_OnOff		0x100
#define LCD_SetupMenu_Relays	0x200
#define LCD_SetupMenu_Sensors	0x300
#define LCD_SetupMenu_Network	0x400
#define LCD_SetupMenu_UpdateFW	0x500
#define LCD_SetupMenu_Relays_Max 8
const char *LCD_SetupMenu[LCD_SetupMenuItems] = { "Exit", "On/Off", "Relays", "Sensors", "Safe Network", "Prepare FW update" };
const char LCD_Str_SetupInfo[] = "Long press OK - Exit";
const char LCD_Str_House[] = "House ";
const char LCD_Str_Boiler[] = "Boiler";
const char LCD_Str_Freq[] = "Freq. ";
const char LCD_Str_HP[] = "HeatPump";
const char LCD_Str_On[] = "ON";
const char LCD_Str_Off[] = "OFF";
const char LCD_Str_SafeNework[] = "OK - SafeNetwork";
const char LCD_Str_PrepareUpdate[] = "OK - Prepare update";
#endif
#define MODBUS_PORT_NUM      Serial2        // Аппаратный порт куда прицеплен Modbus
#define MODBUS_PORT_SPEED    9600           // Скорость порта куда прицеплен частотник и счетчик
#define MODBUS_PORT_CONFIG   SERIAL_8N1     // Конфигурация порта куда прицеплен частотник и счетчик
#define MODBUS_TIME_WAIT     2000           // Время ожидания захвата мютекса для modbus мсек
#define MODBUS_TIME_TRANSMISION 4           // Пауза (msec) между запросом и ответом по модбас было 4
#define MODBUS_TIMEOUT       100			// Таймаут ожидания ответа, мсек
#define MODBUS_MIN_TIME_BETWEEN_TRNS 50		// Минимальная пауза между транзакциями, мсек
#ifdef RADIO_SENSORS
	#if RADIO_SENSORS_PORT == 2
		#define RADIO_SENSORS_SERIAL	Serial2	// Аппаратный порт
	#elif RADIO_SENSORS_PORT == 3
		#define RADIO_SENSORS_SERIAL	Serial3	// Аппаратный порт
	#endif
#endif
#define RADIO_LOST_TIMEOUT	40*60*1000		// через сколько считать, что связь потеряна с датчиком, мсек
#define RADIO_BAT_MIN_V		21				// Минимальное напряжение батарейки датчика, десятые V
#define FC_MODBUS_ADR      1             // Адрес частотного преобразователя на шине не должно совпадать SMD_MODBUS_ADR
#define FC_NUM_READ        5             // Число попыток чтения инвертора (подряд) по модбас до его останова ТН по ошибке ПО УМОЛЧАНИЮ
#define FC_DELAY_REPEAT    10            // мсек Время между ПОВТОРНЫМИ попытками чтения было 100
#define FC_DELAY_READ      10            // мсек Время между последовательными запросами было 20
#define FC_WRITE_READ      10            // мсек Время между последовательной записью
#define FC_ANALOG_RESOLUTION	8		// Bit (8..12)
#define DEFAULT_SDM_SPEED       2400      // Скорость в бодах для счетчика по умолчанию
#define DEFAULT_SDM_MODBUS_ADR  1         // Адрес счетчика на шине не должно совпадать с FC_MODBUS_ADR при программировании инвертор ОКЛЮЧИТЬ (адрес 1)
#define SDM_SPEED           2              // скорость счетчика в константах 0 = 2400 bps. 1 = 4800 bps. 2 = 9600 bps 5=1200 bps  Скорости обмена должны совпадать см MODBUS_PORT_SPEED
#define SDM_MODBUS_ADR      2              // Адрес счетчика на шине не должно совпадать с FC_MODBUS_ADR
#define SDM_READ_PERIOD     (10*1000)      // Время опроса счетчика в мск
#define SDM_NUM_READ        4              // Число попыток чтения счетчика (подряд) по модбас до его отключения (ошибка не генерится)
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

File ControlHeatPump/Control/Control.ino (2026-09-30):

/*
 * Copyright (c) 2016-2026 by Vadim Kulakov vad7@yahoo.com, vad711
 * &                       by Pavel Panfilov <firstlast2007@gmail.com> pav2000
 * "Народный контроллер" для тепловых насосов.
 * Данное програмноое обеспечение предназначено для управления
 * различными типами тепловых насосов для отопления и ГВС.
 *
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
 * This file is distributed in the hope that it will be useful,
 * but WITHOUT ANY WARRANTY; without even the implied warranty of
 * MERCHANTABILITY or FITNESS FOR A PARTICULAR PURPOSE.See the
 * GNU General Public License for more details.
 */
// Последние версии
// https://github.com/vad7/ControlHeatPump - последняя стабильная версия
// Архивные ссылки
// https://github.com/vad7/Arduino-DUE-WireSam  библиотеки доработанные vad711 при релизе добавляются в архив

#include "Arduino.h"
#include "Constant.h"                       // Должен быть первым !!!! кое что берется в стандартных либах для настройки либ, Config.h входит в него

#include <WireSam.h>                        // vad711 доработанная библиотека https://github.com/vad7/Arduino-DUE-WireSam
#include <DS3232.h>                         // vad711 Работа с часами i2c - используются при выключении питания. модифицированная https://github.com/vad7/Arduino-DUE-WireSam
#include <extEEPROM.h>                      // vad711 Работа с eeprom и fram i2c библиотека доработана для DUE!!! https://github.com/vad7/Arduino-DUE-WireSam

#include <SPI.h>                            // SPI - стандартная
#include "SdFat.h"                          // SdFat - модифицированная
#include "FreeRTOS_ARM.h"                   // модифицированная
#include <rtc_clock.h>                      // работа со встроенными часами  Это основные часы!!!
#include <ModbusMaster.h>                   // Используется МОДИФИЦИРОВАННАЯ для омрона мх2 либа ModbusMaster https://github.com/4-20ma/ModbusMaster

// Глубоко переделанные библиотеки
#include <Ethernet.h>                       // Ethernet - модифицированная
#include <Dns.h>                            // DNS - модифицированная
#include <SerialFlash.h>                    // Либа по работе с spi флешом как диском

#include "Hardware.h"
#include "HeatPump.h"
#include "Nextion.h"
#include "Message.h"
#include "Information.h"
#include "MQTT.h"
#include "Statistics.h"
#include "LCD2004.h"
#include "Wattrouter.h"

void vUpdateStepperEEV(void *);
#include "StepMotor.h"

// Семафоры захвата железа
type_SEMAPHORE xModbusSemaphore;                 // Семафор Modbus, инвертор запас на счетчик
#ifdef MODBUS_HEATER_DEDICATED
type_SEMAPHORE xModbusSemaphore2;                // Семафор Modbus шина 2, инвертор запас на счетчик
#else
#define xModbusSemaphore2 xModbusSemaphore
#endif
type_SEMAPHORE xWebThreadSemaphore;              // Семафор сетевой веба и сетевой карты W5500
type_SEMAPHORE xI2CSemaphore;                    // Семафор шины I2C, часы, память, мастер OneWire
uint16_t lastErrorFreeRtosCode;                     // код последней ошибки операционки нужен для отладки
uint32_t startSupcStatusReg;                        // Состояние при старте SUPC Supply Controller Status Register - проверяем что с питание


#if defined(W5500_ETHERNET_SHIELD)                  // Задание имени чипа для вывода сообщений
  const char nameWiznet[] ={"W5500"};
#elif defined(W5200_ETHERNET_SHIELD)
  const char nameWiznet[] ={"W5200"};
#else
  const char nameWiznet[] ={"W5100"};
#endif

// Глобальные переменные
EthernetServer server1(80);                         // сервер
#ifdef MQTT
EthernetClient ethClient(W5200_SOCK_SYS);           // для MQTT
#endif

#ifdef RADIO_SENSORS
void check_radio_sensors(void);
void radio_sensor_send(char *cmd);
#endif

#ifdef MQTT                                 // признак использования MQTT
#include <PubSubClient.h>                   // передаланная под многозадачность  http://knolleary.net
PubSubClient w5200_MQTT(ethClient);  	    // клиент MQTT
#endif

// I2C eeprom Размер в килобитах, число чипов, страница в байтах, адрес на шине, тип памяти:
extEEPROM eepromI2C(I2C_SIZE_EEPROM,I2C_MEMORY_TOTAL/I2C_SIZE_EEPROM,I2C_PAGE_EEPROM,I2C_ADR_EEPROM,I2C_FRAM_MEMORY);
#ifdef USE_RC_CLOCK_SOURCE
RTC_clock rtcSAM3X8(RC);                                               // Внутренние часы, используется внутренний RC генератор
#else
RTC_clock rtcSAM3X8(XTAL);                                               // Внутренние часы, используется часовой кварц
#endif
DS3232  rtcI2C;                                                          // Часы 3231 на шине I2C
static Journal  journal;                                                 // системный журнал, отдельно т.к. должен инициализоваться с начала старта
static HeatPump HP;                                                      // Класс тепловой насос (в констукторе плохо проходит инициализация пинов????)
SdFat card;                                                              // Карта памяти
#ifdef NEXTION   
Nextion myNextion;                                                     // Дисплей
#endif

// Use the Arduino core to set-up the unused USART2 on Serial4 (without serial events)
#ifdef USE_SERIAL4
RingBuffer rx_buffer5;
RingBuffer tx_buffer5;
USARTClass Serial4(USART2, USART2_IRQn, ID_USART2, &rx_buffer5, &tx_buffer5);
//void serialEvent4() __attribute__((weak));
//void serialEvent4() { }
void USART2_Handler(void)   // Interrupt handler for UART2
{
	Serial4.IrqHandler();     // In turn calls on the Serial2 interrupt handler
}
#endif


// Структура для хранения одного сокета, нужна для организации многопотоковой обработки
#define fABORT_SOCK   0                     // флаг прекращения передачи (произошел сброс сети)
#define fUser         1                     // Признак идентификации как обычный пользователь (нужно подменить файл меню)

struct type_socketData
  {
    EthernetClient client;                  // Клиент для работы с потоком
    byte inBuf[W5200_MAX_LEN];              // буфер для работы с w5200 (входной запрос)
    char *inPtr;                            // указатель в входном буфере с именем файла или запросом (копирование не делаем)
    char outBuf[3*W5200_MAX_LEN];           // буфер для формирования ответа на запрос и чтение с карты
    int8_t sock;                            // сокет потока -1 свободный сокет
    uint8_t flags;                          // Флаги состояния потока
    uint16_t http_req_type;                 // Тип запроса
  };
static type_socketData Socket[W5200_THREAD];   // Требует много памяти 4*W5200_MAX_LEN*W5200_THREAD=24 кб

// Установка вачдога таймера вариант vad711 - адаптация для DUE 1.6.11
// WDT_TIME период Watchdog таймера секунды но не более 16 секунд!!! ЕСЛИ WDT_TIME=0 то Watchdog будет отключен!!!
volatile unsigned long ulHighFrequencyTimerTicks;   // vad711 - адаптация для DUE 1.6.11
void watchdogSetup(void)
{
#if WDT_TIME == 0
	watchdogDisable();
#else 
	watchdogEnable(WDT_TIME * 1000);
#endif
}

__attribute__((always_inline)) inline void _delay(int t) // Функция задержки (мсек) в зависимости от шедулера задач FreeRtos
{
  if(xTaskGetSchedulerState() == taskSCHEDULER_RUNNING) vTaskDelay(t/portTICK_PERIOD_MS);
  else delay(t);
}

// Called in delay(), weak
void yield(void)
{
	if(xTaskGetSchedulerState() == taskSCHEDULER_RUNNING) taskYIELD();
}

// Остановить шедулер задач, возврат 1, если получилось
uint8_t TaskSuspendAll(void) {
	if(xTaskGetSchedulerState() == taskSCHEDULER_RUNNING) {
		vTaskSuspendAll(); // запрет других задач
		return 1;
	}
	return 0;
}

void vWeb0(void *) __attribute__((naked));
void vWeb1(void *) __attribute__((naked));
void vWeb2(void *) __attribute__((naked));
void vWeb3(void *) __attribute__((naked));
void vReadSensor(void *) __attribute__((naked));
void vUpdate( void * ) __attribute__((naked));
void vUpdateEEV(void *) __attribute__((naked));
void vUpdateStepperEEV(void *) __attribute__((naked));
void vServiceHP(void *) __attribute__((naked));

void setup() {
	// 1. Инициализация
	// Баг разводки дуе (вероятность). Есть проблема с инициализацией spi.  Ручками прописываем
	// https://groups.google.com/a/arduino.cc/forum/#!topic/developers/0PUzlnr7948
	// http://forum.arduino.cc/index.php?topic=243778.0;nowap
	//pinMode(PIN_SPI_SS0,INPUT_PULLUP);          // Eth Pin 77
	//pinMode(PIN_SPI_SS1,INPUT_PULLUP);          // SD Pin  87
	pinMode(PIN_SPI_CS_SD,INPUT_PULLUP);        // сигнал CS управление SD картой
	pinMode(PIN_SPI_CS_W5XXX,INPUT_PULLUP);     // сигнал CS управление сетевым чипом
#ifdef USE_SERIAL4
	PIO_Configure(PIOB,	PIO_PERIPH_A, PIO_PB20A_TXD2 | PIO_PB21A_RXD2, PIO_DEFAULT);	// Отключаются: A11(AD13)/D65 и D52(AD14)
#endif
#ifdef SPI_FLASH
	pinMode(PIN_SPI_CS_FLASH,INPUT_PULLUP);     // сигнал CS управление чипом флеш памяти
	//pinMode(PIN_SPI_CS_FLASH,OUTPUT);           // сигнал CS управление чипом флеш памяти
#endif
	SPI_switchAllOFF();                         // Выключить все устройства на SPI

#ifdef POWER_CONTROL                        // Включение питания платы если необходимо НАДП здесь, иначе I2C память рабоать не будет
	pinMode(PIN_POWER_ON,OUTPUT);
	digitalWriteDirect(PIN_POWER_ON, LOW);
#endif

	// Настройка сервисных выводов
	pinMode(PIN_KEY1, INPUT_PULLUP);        // Кнопка 1
	pinMode(PIN_BEEP, OUTPUT);              // Выход на пищалку
	pinMode(PIN_LED_OK, OUTPUT);            // Выход на светодиод мигает 0.5 герца - ОК  с частотой 2 герца ошибка
	digitalWriteDirect(PIN_BEEP,LOW);       // Выключить пищалку
	digitalWriteDirect(PIN_LED_OK,HIGH);    // Выключить светодиод
#ifdef USE_REMOTE_WARNING
	pinMode(RWARN_PIN, INPUT_PULLUP);
#endif

#ifndef DEBUG
	if(ret)
#endif

#ifdef DEBUG_NATIVE_USB
	SerialUSB.begin(UART_SPEED);
	dbgPtr = &SerialUSB;
	//if(SerialUSB.lineState()) dbgPtr = &SerialUSB;		// Отладка в Native USB порт, если он подключен
	//else {
		Serial.begin(UART_SPEED);			// Если надо инициализировать отладочный порт
		// Отключить питание (VUSB) на Native USB
		Set_bits(UOTGHS->UOTGHS_CTRL, UOTGHS_CTRL_VBUSHWC);
		PIO_Configure(PIOB, PIO_OUTPUT_0, PIO_PB10A_UOTGVBOF, PIO_DEFAULT);
		PIOB->PIO_CODR = PIO_PB10A_UOTGVBOF; // =0
		//
	}
#else
	Serial.begin(UART_SPEED);				// Если надо инициализировать отладочный порт
	// Отключить питание (VUSB) на Native USB
	Set_bits(UOTGHS->UOTGHS_CTRL, UOTGHS_CTRL_VBUSHWC);
	PIO_Configure(PIOB, PIO_OUTPUT_0, PIO_PB10A_UOTGVBOF, PIO_DEFAULT);
	PIOB->PIO_CODR = PIO_PB10A_UOTGVBOF; // =0
	//
#endif

	// Борьба с зависшими устройствами на шине  I2C (в первую очередь часы) неудачный сброс
	if(!Check_I2C_bus()) Recover_I2C_bus(false);
	Wire.begin();

	// 2. Инициализация журнала
	uint8_t b;
	uint8_t ret = eepromI2C.read(I2C_COUNT_EEPROM, &b, 1);
	if(ret == 0 && b != I2C_COUNT_EEPROM_HEADER && b != 0xFF) {
#ifndef TEST_BOARD
		if(b == 0xAA) {
			if(!eepromI2C.read(I2C_SETTING_EEPROM + 2 + 1, &b, 1) && b < 147) goto xRewriteHeader;
		}
#endif
		ret = 0xFF;
	}
#ifdef LCD2004
	lcd.begin(LCD_COLS, LCD_ROWS); // Setup: cols, rows
	lcd.print("HeatPump v");
	lcd.print(VERSION);
	lcd.setCursor(0, 1);
	lcd.print("(C) vad7@yahoo.com");
	lcd.setCursor(0, 2);
	lcd.print("CFG: ");
	lcd.print(CONFIG_NAME);
	lcd.setCursor(0, 3);
	lcd.print("Loading...");
#endif
	while(ret) {
		SerialDbg.print("Wrong I2C EEPROM or setup, press KEY[D");
		SerialDbg.print(PIN_KEY1);
		SerialDbg.println("->GND] to continue...");
		if(!digitalReadDirect(PIN_KEY1)) {
			WDT_Restart(WDT);
#ifndef TEST_BOARD
xRewriteHeader:
#endif
			b = I2C_COUNT_EEPROM_HEADER;
			ret = eepromI2C.write(I2C_COUNT_EEPROM, &b, 1);
			if(ret) {
				SerialDbg.print("Error ");
				SerialDbg.print(ret);
				SerialDbg.println(" write to EEPROM!");
#ifdef TEST_BOARD
				break;
#endif
			} else SerialDbg.println("Wait...");
			while(1) ;
		}
		for(uint8_t i = 0; i < 1000 / TIME_LED_ERR; i++) {
			digitalWriteDirect(PIN_BEEP, i & 1);
			digitalWriteDirect(PIN_LED_OK, i & 1);
			delay(TIME_LED_ERR);
		}
	}
#ifdef TEST_BOARD
	_delay(1); // Если зависает при загрузке (START...START...) - включить или выключить эту строку
#endif
	journal.Init();
#ifdef POWER_CONTROL
	delay(200);  // Не понятно но без нее иногда на старте срабатывает вачдог.  возможно проблема с буфером
#endif
#ifdef DEMO
	journal.jprintf("DEMO - DEMO - DEMO - DEMO - DEMO - DEMO - DEMO\n");
#endif
#ifdef TEST_BOARD
	journal.jprintf("\n---> TEST BOARD!!!\n\n");
#endif
	journal.jprintf("Config: %s\n", CONFIG_NAME);
	journal.jprintf("Firmware version: %s\n", VERSION);
	showID();                                                                  // информация о чипе
	getIDchip((char*)Socket[0].inBuf);
	journal.jprintf("Chip ID SAM3X8E: %s\n", Socket[0].inBuf);// информация об серийном номере чипа
	if(GPBR->SYS_GPBR[0] & 0x80000000) GPBR->SYS_GPBR[0] = 0; else GPBR->SYS_GPBR[0] |= 0x80000000; // очистка старой причины
	lastErrorFreeRtosCode = GPBR->SYS_GPBR[0] & 0x7FFFFFFF;         // Сохранение кода ошибки при страте (причину перегрузки)
	journal.jprintf("Last reason for reset SAM3x: %s\n", ResetCause());
	journal.jprintf("Last FreeRTOS task + error: 0x%04x", lastErrorFreeRtosCode);
	if(GPBR->SYS_GPBR[4]) journal.jprintf(" (%d)", GPBR->SYS_GPBR[4]);
	if(GPBR->SYS_GPBR[5]) journal.jprintf(" Web(%d)", GPBR->SYS_GPBR[5]);
	journal.jprintf("\n");

#ifdef PIN_LED1                            // Включение (точнее индикация) питания платы если необходимо
	pinMode(PIN_LED1,OUTPUT);
	digitalWriteDirect(PIN_LED1, HIGH);
#endif
#ifdef POWER_CONTROL
	journal.jprintf("Power +5V, +3.3V on board: ON\n");
#endif

	SupplyMonitorON(SUPC_SMMR_SMTH_3_0V);           // включение монитора питания

#ifdef DRV_EEV_L9333                     // Контроль за работой драйвера ЭРВ
	pinMode(PIN_STEP_DIAG,INPUT_PULLUP);
	journal.jprintf("Control EEV driver L9333: ON \n");
#endif

#ifdef RADIO_SENSORS
	RADIO_SENSORS_SERIAL.begin(RADIO_SENSORS_PSPEED, RADIO_SENSORS_PCONFIG);
#endif

	// 3. Инициализация и проверка шины i2c
	journal.jprintf("1. Setting and checking I2C devices . . .\n");

	uint8_t eepStatus=0;
#ifdef I2C_EEPROM_64KB
	if(journal.get_err()) { // I2C память и журнал в ней уже пытались инициализировать
#endif
		Wire.begin();
		for(uint8_t i=0; i<I2C_NUM_INIT; i++ )
		{
			if ((eepStatus=eepromI2C.begin(I2C_SPEED))>0)    // переходим на I2C_SPEED и пытаемся инициализировать
			{
				journal.jprintf("$ERROR - I2C mem failed, status = %d\n", eepStatus);
#ifdef POWER_CONTROL
				digitalWriteDirect(PIN_POWER_ON, HIGH);
				digitalWriteDirect(PIN_LED1, LOW);
				_delay(2000);
				digitalWriteDirect(PIN_POWER_ON, LOW);
				digitalWriteDirect(PIN_LED1, HIGH);
				_delay(500);
				Wire.begin();
#else
				Wire.begin();
				_delay(500);
#endif
				WDT_Restart(WDT);                       // Сбросить вачдог
			}  else break;   // Все хорошо
		} // for
#ifdef I2C_EEPROM_64KB
	}
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
void loop() {}

//  З А Д А Ч И -------------------------------------------------
// Это и есть поток с минимальным приоритетом измеряем простой процессора
//extern "C" 
//{
static bool Error_Beep_confirmed = false;

extern "C" void vApplicationIdleHook(void)  // FreeRTOS expects C linkage
{
	static unsigned long countLED = 0;
	static unsigned long countBeep = 0;

	WDT_Restart(WDT);                                                            // Сбросить вачдог
	register unsigned long ticks = GetTickCount();
//	static unsigned long cpu_idle_max_count = 0; // 1566594 // максимальное значение счетчика, вычисляется при калибровке и соответствует 100% CPU idle
//	static unsigned long ulIdleCycleCount = 0;
//	ulIdleCycleCount++;                                                          // приращение счетчика
//	if(ticks - countLastTick >= 3000)		// мсек
//	{
//		countLastTick = ticks;                            // расчет нагрузки
//		if(ulIdleCycleCount > cpu_idle_max_count) cpu_idle_max_count = ulIdleCycleCount; // это калибровка запоминаем максимальные значения
//		HP.CPU_IDLE = (100 * ulIdleCycleCount) / cpu_idle_max_count;              // вычисляем текущую загрузку
//		ulIdleCycleCount = 0;
//	}
	// Светодиод мигание в зависимости от ошибки и подача звукового сигнала при ошибке
	if(HP.get_errcode() != OK) {          // Ошибка
		if(ticks - countLED > TIME_LED_ERR) {
			digitalWriteDirect(PIN_LED_OK, !digitalReadDirect(PIN_LED_OK));
			countLED = ticks;
		}
		if(HP.get_Beep() && !Error_Beep_confirmed && ticks - countBeep > TIME_BEEP_ERR) {
			digitalWriteDirect(PIN_BEEP, !digitalReadDirect(PIN_BEEP)); // звуковой сигнал
			countBeep = ticks;
		}
	} else if(ticks - countLED > TIME_LED_OK) {   // Ошибок нет и время пришло
		Error_Beep_confirmed = false;
		digitalWriteDirect(PIN_BEEP, LOW);
		digitalWriteDirect(PIN_LED_OK, !digitalReadDirect(PIN_LED_OK));
		countLED = ticks;
	}
	pmc_enable_sleepmode(0);
}

// --------------------------- W E B ------------------------
#define WEB_SERVER_TASK(n) {\
	if(SemaphoreTake(xWebThreadSemaphore, 0)) {\
		/*WEB_STORE_DEBUG_INFO(1);*/\
		web_server(n);\
		SemaphoreGive(xWebThreadSemaphore);\
		vTaskDelay(TIME_WEB_SERVER);\
		/*WEB_STORE_DEBUG_INFO(2);*/\
	} else vTaskDelay(1);\
}
// Задача обслуживания web сервера
// Сюда надо пихать все что связано с сетью иначе конфликты не избежны
// Здесь также обслуживается посылка уведомлений MQTT
// Первый поток веб сервера - дополнительно нагружен различными сервисами
void vWeb0(void *)
{ //const char *pcTaskName = "Web server is running\r\n";
	static unsigned long pingt, resW5200, iniW5200, _other_tasks;
	pingt = resW5200 = iniW5200 = _other_tasks = xTaskGetTickCount();
#ifdef WR_CHECK_Vbat_INSTEAD_OF_MPPT_SIGN
	static unsigned long check_vbat_time = rtcSAM3X8.unixtime();
#endif
#ifdef HTTP_LowConsumeRequest
	static uint16_t RepeatLowConsumeRequest = 0;
#endif
#ifdef WEATHER_FORECAST
	static uint8_t WF_Day = 0;
#endif
#if defined(HTTP_MAP_RELAY_MAX) && defined(HTTP_MAP_Server)
	static uint32_t daily_http_time = 0;
#endif
#ifdef MQTT
	static unsigned long narmont=0;
	static unsigned long mqttt=0;
#endif
	HP.timeNTP = xTaskGetTickCount();        // В первый момент не обновляем
#ifndef WR_PowerMeter_Modbus
	Web0_FreqTime = xTaskGetTickCount();
#endif
	static bool network_last_link = true;
	for(;;)
	{
		if(SemaphoreTake(xWebThreadSemaphore, 0)) {
			web_server(MAIN_WEB_TASK);
			SemaphoreGive(xWebThreadSemaphore);
			vTaskDelay(TIME_WEB_SERVER);
			if(HP.message.sendMessage()) {  // Отработать отсылку сообщений (внутри скрыта задержка после включения)
				vTaskDelay(TIME_WEB_SERVER);
			}
		} else vTaskDelay(1);

		bool active = true;   // ФЛАГ Одно дополнительное действие за один цикл - распределяем нагрузку, если действие проделано то active = false и новый цикл

#ifdef WR_PowerMeter_Modbus		// Синхронизируемся с чтением счетчика - сразу после
		if(WR_PowerMeter_New) {
			WR_PowerMeter_New = false;
#else
		if(xTaskGetTickCount() - Web0_FreqTime > WEB0_FREQUENT_JOB_PERIOD) {
			Web0_FreqTime = xTaskGetTickCount();
#endif
#ifdef HTTP_LowConsumeRequest
			if(active) {
				if(GETBIT(HP.Option.flags, fBackupPower) != Request_LowConsume || (RepeatLowConsumeRequest && --RepeatLowConsumeRequest == 0)) {
					strcpy(Socket[MAIN_WEB_TASK].outBuf, HTTP_LowConsumeRequest);
					_itoa(GETBIT(HP.Option.flags, fBackupPower), Socket[MAIN_WEB_TASK].outBuf + sizeof(HTTP_LowConsumeRequest)-1);
					int err = Send_HTTP_Request(HTTP_LowConsumeServer, WebSec_Microart.hash, Socket[MAIN_WEB_TASK].outBuf, false);
					if(err != -2000000000) {
						if(err > -2000000000) Request_LowConsume = GETBIT(HP.Option.flags, fBackupPower);
						else RepeatLowConsumeRequest = (uint16_t)(HTTP_REQUEST_ERR_REPEAT * 1000 / WEB0_OTHER_JOB_PERIOD + 1);
					}
				}
			}
#endif
#ifdef WATTROUTER
			WR_Process();
#endif

		} else if(xTaskGetTickCount() - _other_tasks > WEB0_OTHER_JOB_PERIOD) { // Другие задачи

			_other_tasks = xTaskGetTickCount();                 // Запомнить тики
			active = HP.message.dnsUpdate();                // Обновить адреса через dns если надо, dnsUpdate() возвращает true если обновления не было
#ifdef MQTT
			if(active) active = HP.clMQTT.dnsUpdate();                             // Обновить адреса через dns если надо для MQTT если обновления не было то возвращает true
#endif

#ifdef WEATHER_FORECAST
			if(active && rtcSAM3X8.get_days() != WF_Day) {
				WF_BoilerTargetPercent = 0;
				if(rtcSAM3X8.get_hours() == WR.WF_Time / 10 && rtcSAM3X8.get_minutes() >= (WR.WF_Time % 10) * 10 && strlen(HP.Option.WF_ReqServer)) {
					int err = Send_HTTP_Request(HP.Option.WF_ReqServer, NULL, HP.Option.WF_ReqText, 4);
					if(err == OK) err = WF_ProcessForecast(Socket[MAIN_WEB_TASK].outBuf);
					if(err == OK) WF_Day = rtcSAM3X8.get_days();
					else {
						if(rtcSAM3X8.get_minutes() == 59 && rtcSAM3X8.get_seconds() >= 59 - uint8_t(WEB0_OTHER_JOB_PERIOD / 1000)) {
							journal.jprintf_time("WF: Request Error %d\n", err);
							HP.message.setMessage(pMESSAGE_ERROR,(char*)"Ошибка получения прогноза погоды", err);
						}
					}
					active = false;
				}
			}
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

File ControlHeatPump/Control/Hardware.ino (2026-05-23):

/*
 * Copyright (c) 2016-2021 by Vadim Kulakov vad7@yahoo.com, vad711
 * &                       by Pavel Panfilov <firstlast2007@gmail.com> pav2000
 * "Народный контроллер" для тепловых насосов.
 * Данное програмноое обеспечение предназначено для управления
 * различными типами тепловых насосов для отопления и ГВС.
 *
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
 * This file is distributed in the hope that it will be useful,
 * but WITHOUT ANY WARRANTY; without even the implied warranty of
 * MERCHANTABILITY or FITNESS FOR A PARTICULAR PURPOSE.See the
 * GNU General Public License for more details.
 */
// --------------------------------------------------------------------------------
// Описание базовых классов для работы c "железом"
// (датчики и исполнительные устройства) зависит от контроллера
// --------------------------------------------------------------------------------
#include "Hardware.h"
#include "Wattrouter.h"

// --------------------------------------------------------------------------------
// Настройка таймера и ацп для чтения датчика давления
// Зависит от чипа
// --------------------------------------------------------------------------------
// Старт считывания АЦП
void start_ADC()
{
	adc_setup();                                        // setup ADC
	pmc_enable_periph_clk(TC_INTERFACE_ID + 2);         // clock TC0_CHA2, WARNING: interfere with output - analogWrite(58[AD4],n)
	TcChannel * t = TC0->TC_CHANNEL + 2;                // pointer to TC0 registers for its channel 2
	t->TC_CCR = TC_CCR_CLKDIS;                          // disable internal clocking while setup regs
	t->TC_IDR = 0xFFFFFFFF;                             // disable interrupts
	t->TC_SR;                                           // read int status reg to clear pending
	t->TC_CMR = TC_CMR_TCCLKS_TIMER_CLOCK1 |            // use TCLK1 (prescale by 2, = 42MHz)
			TC_CMR_WAVE |                               // waveform mode
			TC_CMR_WAVSEL_UP_RC |                       // count-up PWM using RC as threshold
			TC_CMR_EEVT_XC0 |                           // Set external events from XC0 (this setup TIOB as output)
			TC_CMR_ACPA_CLEAR | TC_CMR_ACPC_SET |		// set clear and set from RA and RC compares
			TC_CMR_BCPB_NONE | TC_CMR_BCPC_NONE;
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

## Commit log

2020-11-30 fix accurate power
2020-12-01 Nextion - show error on main screen
    [Constant.h, Nextion.ino]
2020-12-03 fix pumps in pause
    [Control.ino, HeatPump.h]
2020-12-20 ежесуточные реле - переключение по темперуре и ночью
2021-01-02 fix: пересоздание stats файлов при ошибке последовательности или длине=0
    [Statistics.ino]
2021-01-02 EEV: Установка в позицию бойлера при переходе на лету с отопления
2021-01-02 EEV: Корректировка, если при переходе отопление-бойлер текущая позиция меньше стартовой бойлера
2021-01-10 Статистика - Тэн бойлера
2021-01-10 Не считать STATS_WHEN_WORKD в переходных моментах бойлер-отопление
2021-01-13 fix EEV, Vacon: контроль температуры, авто-сброс ошибки связи
    [Constant.h, Hardware.h, Hardware.ino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]
2021-01-14 Revert "upd readsensor"
    This reverts commit af65440759bff5dbdbd1c805e3bafa6474e2412e.
    [Control.ino]
2021-01-14 Vacon: управление вентилятором, настрока мощности; дамп ячеек Modbus,
2021-01-15 Загрузка файла дампа в устройство Modbus
2021-01-17 ГВС: использовать только тэн во время "расписание только для тена"
2021-01-19 Ограничение частоты инвертора по времени
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2021-01-22 fix расчет COP
    [BOM_I2C_OneWire_2021-01-21.csv]
2021-01-28 fix: задача "Насосы в паузе"
    [Constant.h, Control.ino, VaconFC.ino]
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2021-01-31 Запрет изменени времени через веб во время работы ТН
2021-02-11 исправление безопасного доступа через веб при режиме user без пароля
    [Constant.h, WebServer.ino]
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2021-02-13 begin fix EEV direct
    [Hardware.ino]
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2021-02-23 опция продолжение отопления после нагрева бойлера, если внутри гистерезиса
2021-02-28 motherboard for Arduino DUE
    [Project_Arduino DUE shield - BOM.csv, Project_Arduino DUE shield - PickAndPlace_Board.csv]
2021-03-03 upd board
    [LCSC_Exported_shoping_cart_1.xlsx, PriceCalc.xlsx, Project_Arduino DUE shield - BOM.csv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]
2021-03-04 WR: корректировка минимальной мощности в зависимости текущей мощности панелей
2021-03-06 Работа дневного реле совместно с таким же реле в ваттроутере
2021-03-07 board upd
    [PriceCalc.xlsx, Project_Arduino DUE shield - BOM.csv, Project_Arduino DUE shield - BOM_DS3231-SOIC16.csv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]
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2021-04-22 Перенос настроек ТЭНа ТН и насосов из настроек ТН в отопление
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2021-05-31 fix Насосы в паузе
    [Constant.h, Control.ino, HeatPump.h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]
2021-06-02 WR: Нагрев бойлера во время отсутствия электричества, если есть солнце
2021-06-22 Перенос настройки выключения насоса после останова компрессора в профили
2021-06-24 Работа насосов после останова компрессора вынесена в отдельную задачу
2021-06-26 fix pumps
2021-06-28 Задержка выключения насосов по ошибке и ГВС в общих настройках, фикс генератора
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2021-07-17 fix TEST mode, temp sensors
    [Constant.h, Control.ino, DigitalTemp.ino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]
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2021-07-30 Отображение на плане нагрева бойлера от СК, v.1.154
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2021-11-11 Возможность использовать несколько периодов включения одного и того же ежесуточного реле.
2021-11-12 NTOUT - только во время ночи по температуре
2021-11-27 Возможность задать дополнительно любой датчик температуры как цель отопления
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2021-12-08 догрев бойлера тэном во время паузы компрессора и низкой температуры
2021-12-09 догрев теном, если не смогли нагреть компрессором по t подачи
2021-12-25 Раздельное управление ТП по температуре, Максимальная температура цели, Старт нагрева по минимальной температуре подачи
2021-12-25 Температура цели для теплого пола (управление реле ТП)
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2021-12-31 Nextion - если догрев бойлера тэном, то выводим его
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2022-03-09 upd web - переключение метки календара по клику на левой ячейке или на днях недели
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2022-04-04 fix - выкл. включенные дневные реле при смене профиля
    [Constant.h, Control.ino, HeatPump.h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]
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2022-05-02 WR контроль напряжения на АКБ вместо знака КЭС
2022-07-13 fix WR (SUN sign)
    [Constant.h, Util.ino]
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2022-10-10 Фикс радиодатчиков, все датчики температуры после старта = STARTTEMP
2022-10-17 Обработка пропадания питания во время вызова функций частотника
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2024-02-13 Minimum out temp sensor define for statistics: STATS_TOUT_MIN_OTHER
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2024-04-20 Отображение приходящей мощности от солнечных панелей на схеме
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2024-05-12 показывать предыдущий период между получениями данных от радиодатчиков
2024-07-22 При охлаждение из датчиков температуры с метками "мин" берется с максимальной темпертурой
2024-11-18 Отдельная настройка - задержка выключения насоса бойлера косвенного нагрева, запрет выключения тэна догрева вов ремя работы этого насоса
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2024-12-25 Подсчет потребления по дневному/ночному тарифу раздельно, опциональное логирование энергии со счетчика
2025-03-14 Начало работ по добавлению котла (в т.ч. Opentherm через Modbus)
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2025-05-20 Управление дополнительным котлом, возможность настроить раздельные цели для котла и ТН, рефакторинг кода, исправление ошибок, динамические картинки на схеме
    [Constant.h, Control.ino, DateTime.ino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]
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2025-07-25 единая функция переключение профиля (через останов по необходимости), задержка выключения насосов при ошибке, рефакторинг
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2025-07-30 удалена задача CommandHP, исправлен контроль освобождения семафоров, рефакторинг
    [Constant.h, Control.ino, DateTime.ino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]
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2025-08-08 upd I2C reset
2025-09-02 доработка библиотеки Ethernet - функция RTOS_delay() во время ожидания
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2025-10-20 опция греть бойлер только тэном (температура вне расписания как для догрева)
2025-11-14 Удаленный датчик для информирования (счетчик импульсов) - Код ошибки BMS
2025-12-30 веб - инфа по BMS на закладке ваттроутера
2026-01-07 добавлен yield() в либы для предотвращения блокировки задач
2026-01-20 фиксация максимального разбега ячеек BMS и времени (после '/' в веб)
2026-03-04 опция: Переключаться на другой профиль при попытке пуска компрессора на резервном источнике
2026-03-10 исправление, нагрев бойлера только тэном
    [Constant.h, Hardware.ino, HeatPump.h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]
2026-03-10 изменен гистерезис нагрева бойлера от солнца, графики перенесены в меню Статистика
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2026-03-27 Опциональный прогрев трассы Котла по времени и/или по t (THEATER)
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2026-04-01 вынос ваттроутера в отдельный .INO, подогрев трассы, трехходовой ГВС (не закончено)
2026-04-07 оптимизация, исправление ошибок
2026-04-09 возврат на старый профиль после его переключения на резервном источнике
2026-04-20 опция - не переключать лишний раз R3WAY (бойлер-СО)
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2026-04-27 Уставка подачи котла задается в профилях - Целевая температура подачи
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2026-05-02 исправление и доработка модбаса
    [Constant.h, Control.ino, Hardware.ino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]
2026-05-05 Предварительный нагрев трассы котла по времени и по температуре, отложенное включение теплого пола по температуре
2026-05-06 исправление ошибок
2026-05-07 исправление
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2026-05-13 рефакторинг Modbus, разделение на две шины, изменена библиотека ModbusMaster
2026-05-14 перенос цели температуры дома в переключаемый проифиль, если она была изменена без сохранения
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2026-06-03 исправление графиков
